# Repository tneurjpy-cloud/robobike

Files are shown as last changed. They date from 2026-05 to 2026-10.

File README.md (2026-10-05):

https://github.com/tneurjpy-cloud/robobike
| Supported Targets | ESP32-C3 |
| --- | --- |

ROBOBIKE: Autonomous Self-Balancing Bicycle Robot  
Copyright 2026.06.05    Masayuki Tanaami      Mobile-Bot Lab. Japan  

ESP-IDF components and tools paths depend on installation location  

* Control Logic
The ROBOBIKE utilizes a dual-loop control system: an outer steering PD loop and an inner roll rate feedback loop to achieve self-balancing via counter-steering.

## Control System Architecture

```mermaid
graph TD
    %% 目標値の入力
    In((str_target)) -- "目標値" --> Sum1((+))

    subgraph OuterLoop [外側：ステアリングPD制御]
        Sum1 -- "偏差" --> GainP[Pゲイン]
        Sum1 -- "偏差" --> Diff[微分+LPF]
        
        GainP --> Sum2((+))
        Diff --> Sum2
    end

    Sum2 -- "目標ロール速度" --> Sum3((+))

    subgraph InnerLoop [内側：ロール速度FB]
        IMU[IMU_roll実測] -. "−" .-> Sum3
        Sum3 -- "偏差" --> GainW[ロールゲイン]
        GainW -- "更新量" --> Integ["積分 & 逆操舵<br>(str_out -= 更新量)"]
    end

    %% 出力とフィードバック
    Integ --> OutP[ステアリング出力 str_out]
    OutP -. "フィードバック" .-> Sum1
    
    OutP --> Limit[リミッタ]
    Limit --> PWM((PWM出力))

    %% スタイルの設定
    style OuterLoop fill:#fdfdfd,stroke:#333
    style InnerLoop fill:#f0f7ff,stroke:#0052cc
    style Integ fill:#e1f5fe,stroke:#01579b

```
## Getting Started

This project is based on "Captive Portal Example".  
Development should be done using ESP-IDF v6.0  
Please install the ESP-IDF extension in VS-Code before building this project.  
  
* How to set up IntelliSense in VS Code:  
(1) Install the ESP-IDF Extension.  
(2) (Ctrl+Shift+P)Run the command "ESP-IDF: Add vscode configuration folder".  
(3) Perform a Build to generate necessary configuration files.  
-----------------------------------------------------------  
* Settings from menuconfig are saved to \project\sdkconfig  
* Change via menuconfig, KCONFIG Name:  
    Flash size : 4MB  
    Partition Table : Custom Partition Table CSV  
        CSV file : partitions.csv  
    configUSE_TRACE_FACILITY : checked  
    configGENERATE_RUN_TIME_STATS : checked
    configTICK_RATE_HZ : 100
* For debug with GDB, delete "launch.json"
    Full Clean
    Select Target to esp32c3 via USB JTAG
    Select COM port, Build and flash
    Power down the target and perform a complete system reboot.
    OpenOCD Server, select "Eclipse CDT..."
    Full Clean
    Slelect Target to esp32c3 via USB JTAG
    Select COM port, Build and flash
    Power down the target and perform a complete system reboot.
    OpenOCD Server, select "Eclipse CDT..."
-----------------------------------------------------------  

* Change Log  
```text
Date        CODE    DATA    Description
------------------------------------------------------------------------------------------------
2026.09.27  1042       6    Add: Test mode on every reset
2026.09.13  1041       6    Dbg: Fix mobile file selection issue on OTA
2026.09.11  1040       6    Dbg: Stop servo PWM during OTA
2026.09.10  1038       6    Dbg: Accept OTA by smartphone
2026.09.02  1037       6    Chg: Captive portal handler(for iPhone)
2026.08.28  1036       6    Chg: Sleep time, minor changes for auto circling mode
2026.07.05  1033       4    Add: Data monitor and its related files.
2026.06.05  1032       4    Dbg: LED control configTICK_RATE_HZ:100
2026.05.26  1031       4    Chg: Servo PWM Rising Times. Lo-pass filter T
2026.05.19  1030    1022    Chg: Axis polarity inversion / No use GPIO Int. for Task
                            Dbg: Monitor.html  
2026.05.06  1029    1022    Chg: 3ms 1-shot soft timer -> 4ms espTimer / STR cmd Polarity +: left
                            Add: Ota, Data monitor.
                            Chg: esp-idf v5.4.1-->> v6.0.1
2026.04.07  1028    1022    Add: WiFi AP Ch. randomize
2026.03.31  1027    1021    Add: BACK cmd, SV EN Cont. heapless buffer
2026.03.20  1025    1021    Mov: GPIO definitions from servo.c to userdefine.h
2026.03.01  1024    1021    Add: IMU data API, 
                            Dbg: Calibration
2026.02.09  1023    1021    Add: Auto circling On/Off, restore SLEEP function
2026.01.20  1022    1021    Add: Speed buttons to control UI, add only_data
2026.01.17  1021    1021    Add: Auto circling
2026.01.11  1020    1020    The 1st release
2025.12.10  1017    1015    Ex1 step: converted to float (smooth side stand movement)
2025.11.29  1016    1015    Add: Steering slide bar
2025.11.11  1014    1014    Suppress UI scaling, add adjustment items, update stop sequence
2025.10.28  1011    1011    Update: Adjustment screen
```

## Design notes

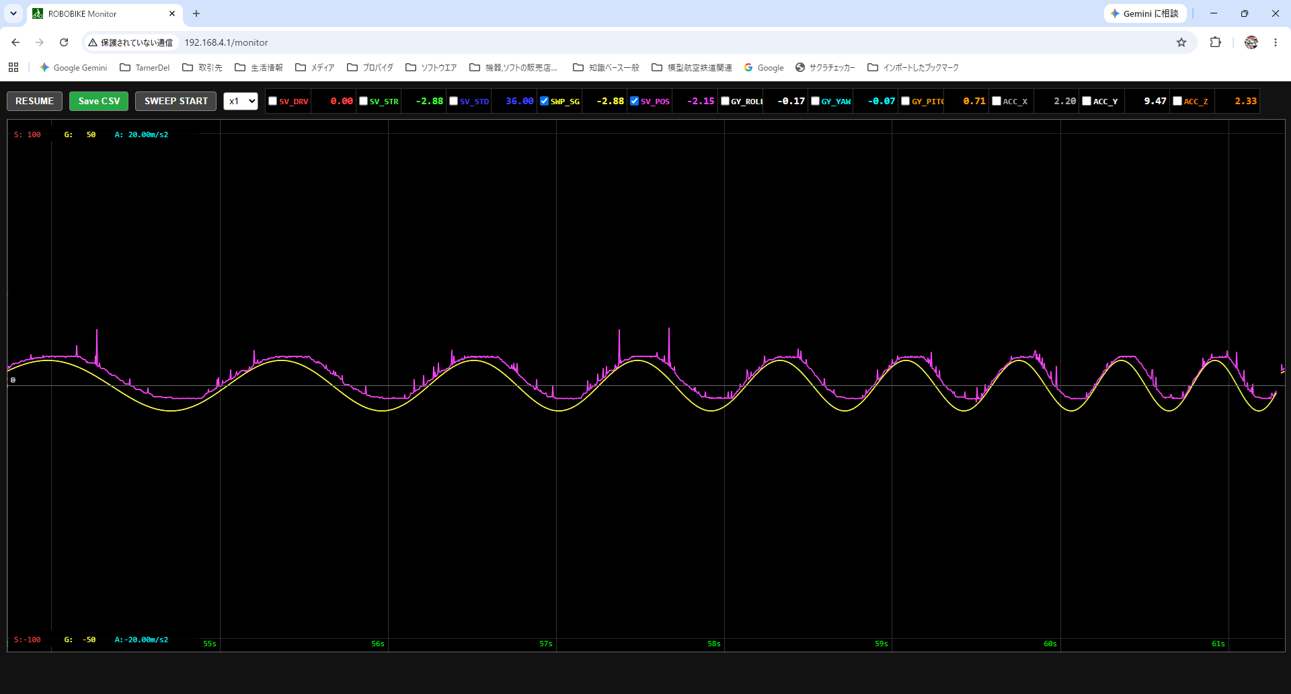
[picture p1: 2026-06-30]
doc/monitor.png

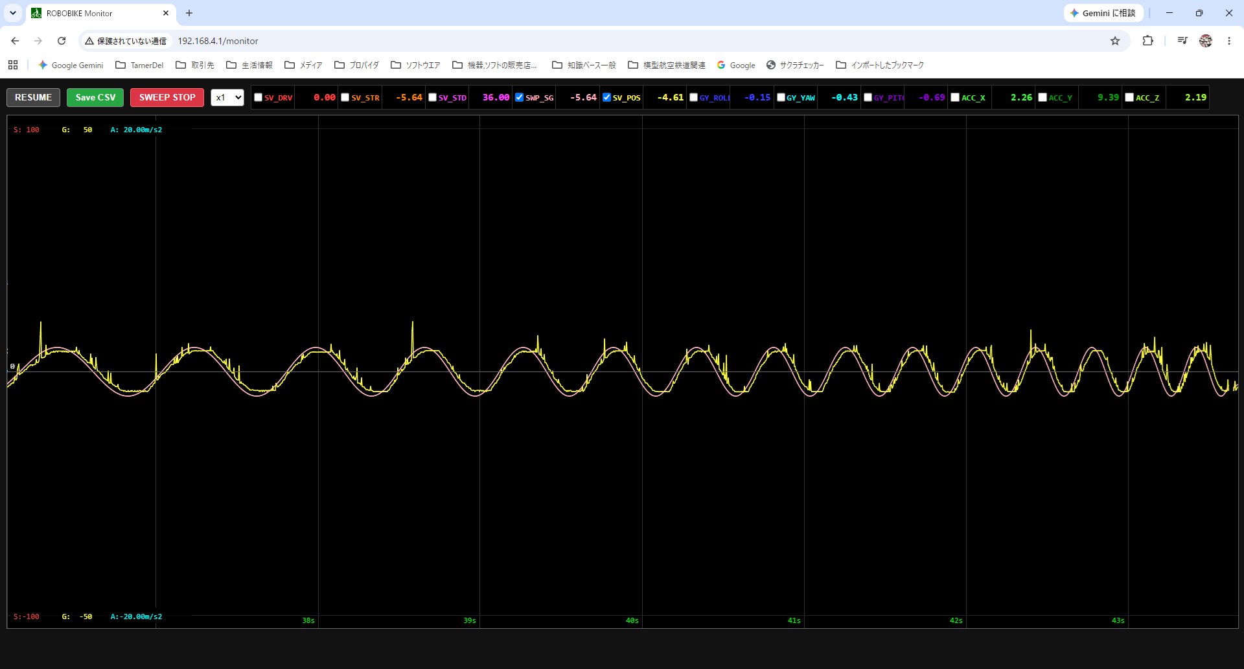
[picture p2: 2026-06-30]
doc/monitor2.png

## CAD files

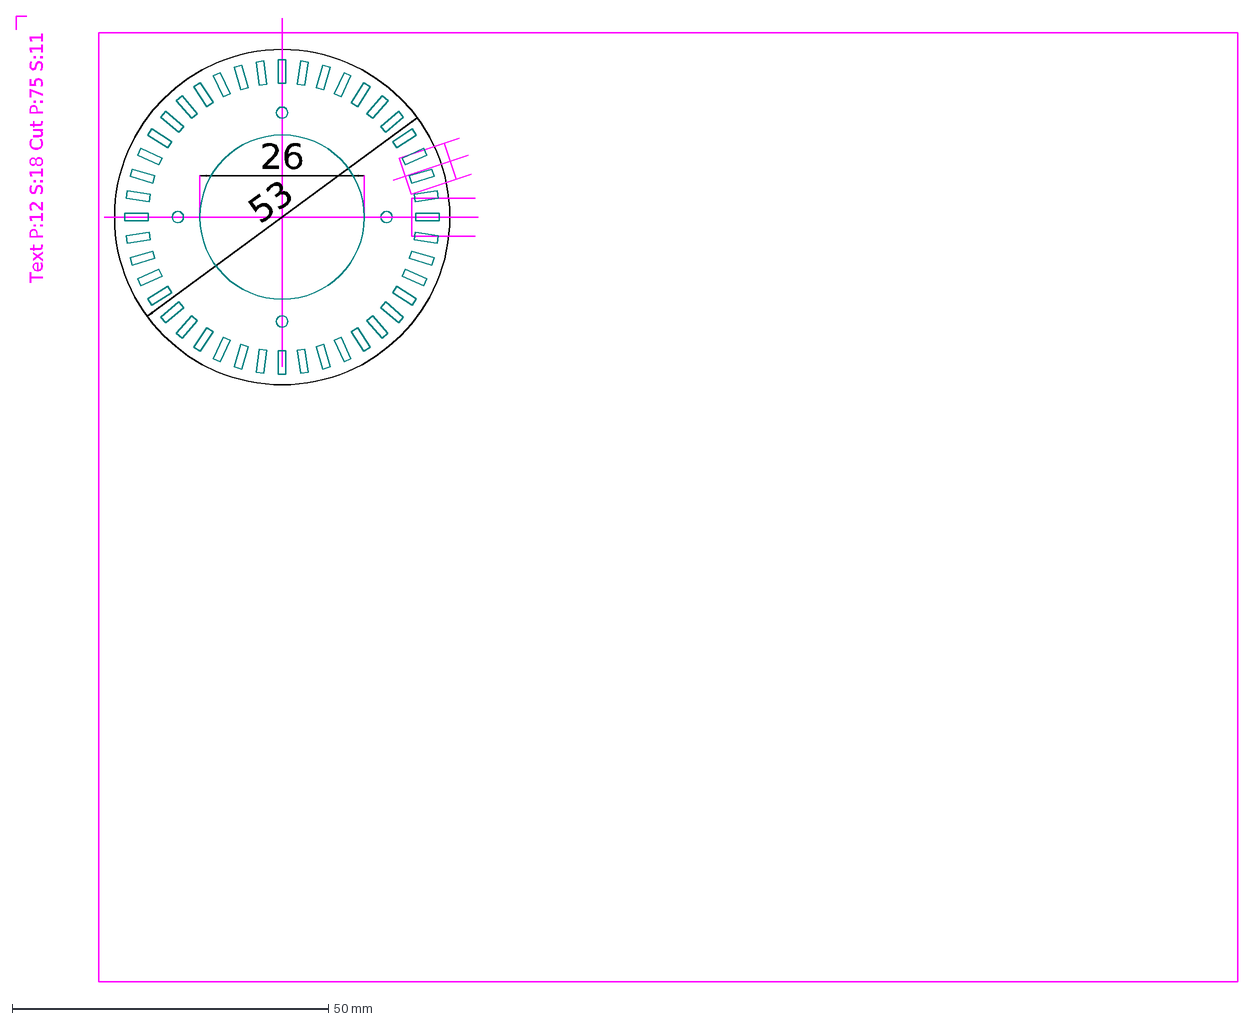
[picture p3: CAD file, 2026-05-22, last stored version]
hardware/DXF/slitring.dxf
Text P:12 S:18 Cut P:75 S:11
53
26

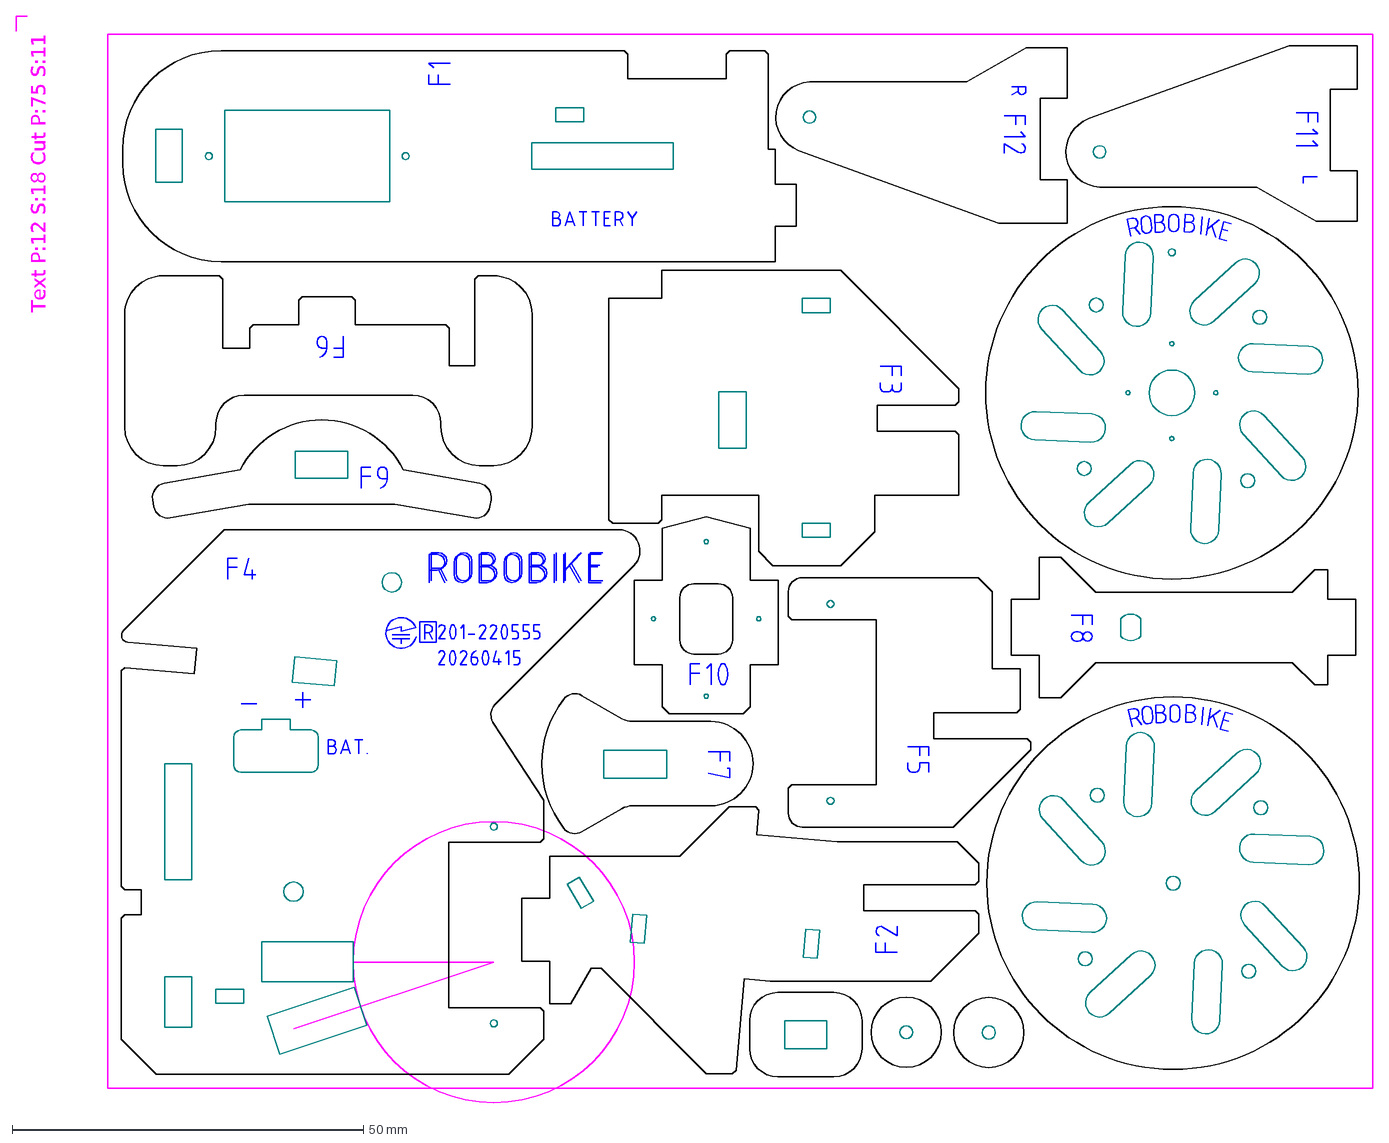
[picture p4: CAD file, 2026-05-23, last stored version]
hardware/DXF/20260522_1p.dxf
Text P:12 S:18 Cut P:75 S:11

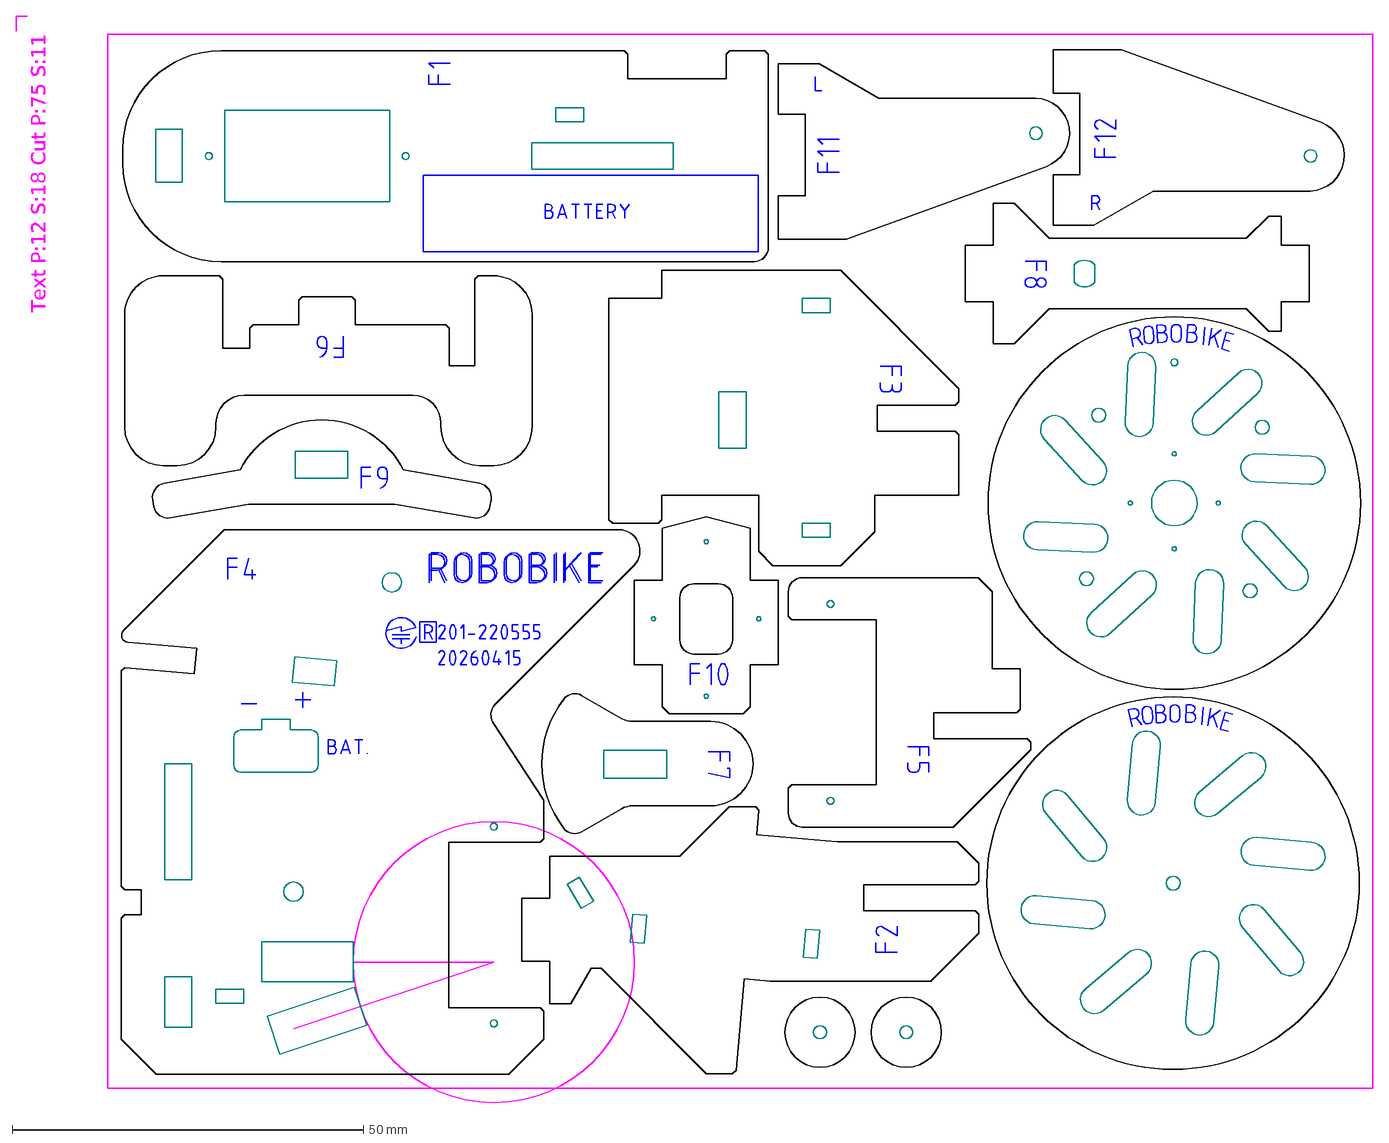
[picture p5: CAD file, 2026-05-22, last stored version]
hardware/DXF/20260407_1p.dxf
Text P:12 S:18 Cut P:75 S:11

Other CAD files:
hardware/DXF/#20260522_1p.dxf

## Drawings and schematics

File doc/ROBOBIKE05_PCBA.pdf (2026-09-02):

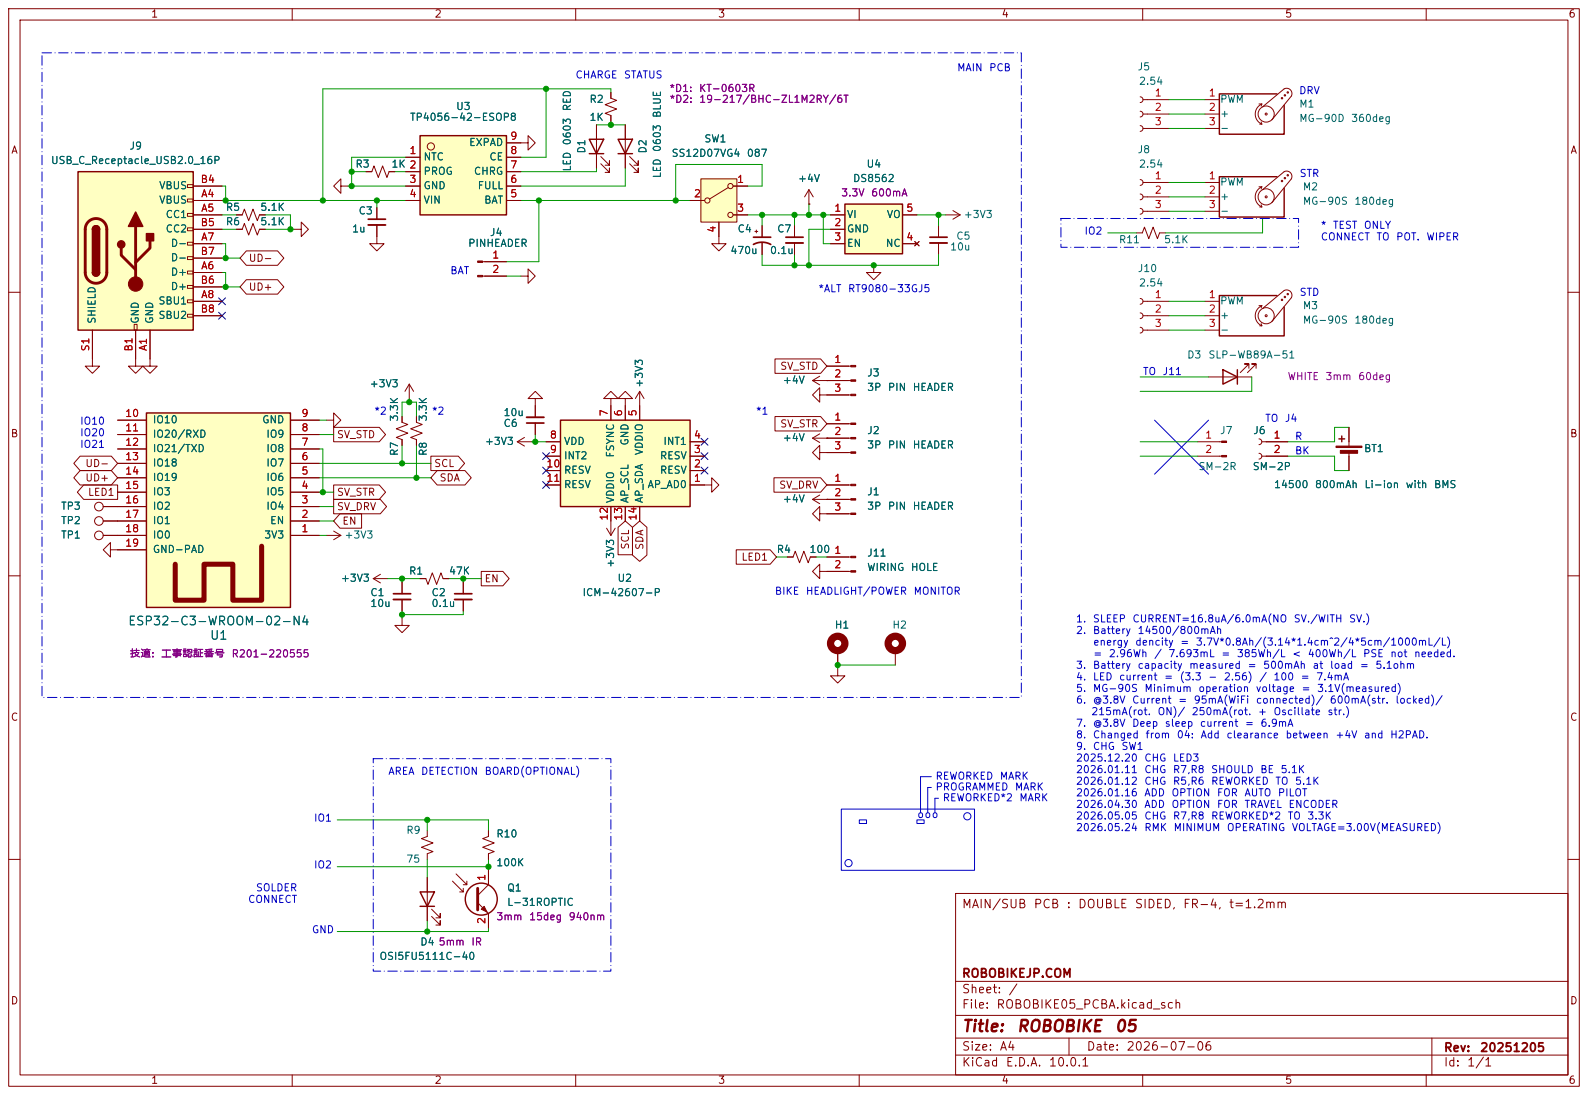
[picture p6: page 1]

* TEST ONLY CONNECT TO POT. WIPER

BIKE HEADLIGHT/POWER MONITOR

1. SLEEP CURRENT=16.8uA/6.0mA(NO SV./WITH SV.) 2. Battery 14500/800mAh

energy dencity = 3.7V*0.8Ah/(3.14*1.4cm^2/4*5cm/1000mL/L) = 2.96Wh / 7.693mL = 385Wh/L < 400Wh/L PSE not needed. 3. Battery capacity measured = 500mAh at load = 5.1ohm

4. LED current = (3.3 - 2.56) / 100 = 7.4mA 5. MG-90S Minimum operation voltage = 3.1V(measured) 6. @3.8V Current = 95mA(WiFi connected)/ 600mA(str. locked)/

215mA(rot. ON)/ 250mA(rot. + Oscillate str.) 7. @3.8V Deep sleep current = 6.9mA 8. Changed from 04: Add clearance between +4V and H2PAD. 9. CHG SW1

2025.12.20 CHG LED3
2026.01.11 CHG R7,R8 SHOULD BE 5.1K
2026.01.12 CHG R5,R6 REWORKED TO 5.1K
2026.01.16 ADD OPTION FOR AUTO PILOT 2026.04.30 ADD OPTION FOR TRAVEL ENCODER

2026.05.05 CHG R7,R8 REWORKED*2 TO 3.3K
2026.05.24 RMK MINIMUM OPERATING VOLTAGE=3.00V(MEASURED)

MAIN/SUB PCB : DOUBLE SIDED, FR-4, t=1.2mm

Size: A4 | Rev: 20251205
KiCad E.D.A. 10.0.1 | Id: 1/1

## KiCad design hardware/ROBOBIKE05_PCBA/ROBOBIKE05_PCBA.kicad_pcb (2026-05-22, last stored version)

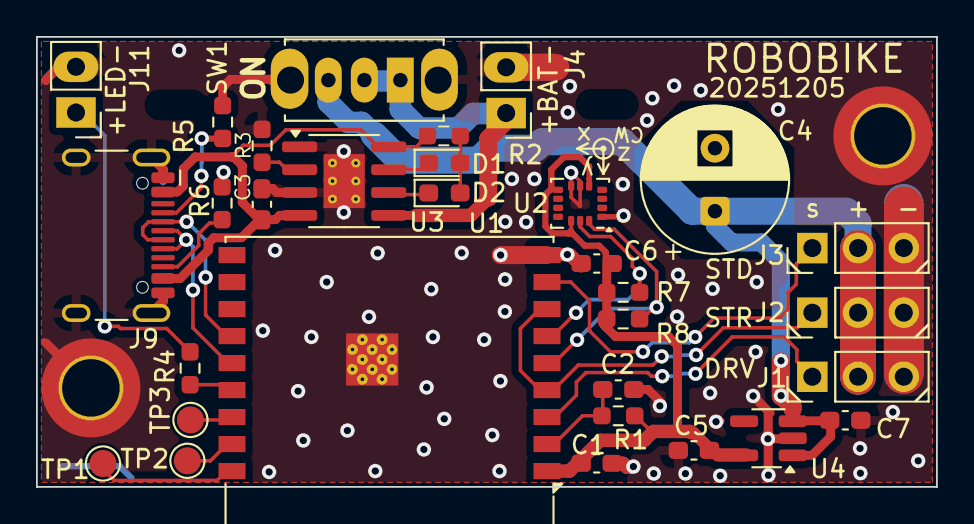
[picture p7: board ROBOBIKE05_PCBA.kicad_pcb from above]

Board: 2 copper layers, 50.0 x 25.0 mm, 33 parts (0 on the bottom side), 24 nets.

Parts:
C1, C5, C6: 10u; C_0603_1608Metric_Pad1.08x0.95mm_HandSolder
C2, C7: 0.1u; C_0603_1608Metric_Pad1.08x0.95mm_HandSolder
C3: 1u; C_0603_1608Metric_Pad1.08x0.95mm_HandSolder
C4: 470u; CP_Radial_D8.0mm_P3.50mm
D1: LED 0603 RED; LED_0603_1608Metric_Pad1.05x0.95mm_HandSolder
D2: LED 0603 BLUE; LED_0603_1608Metric_Pad1.05x0.95mm_HandSolder
H1, H2: MountingHole_Pad; MountingHole_3.2mm_M3_ISO14580_Pad_TopBottom
J1, J2, J3: 3P PIN HEADER; PinHeader_1x03_P2.54mm_Vertical
J4, J11: WIRING HOLE; PinHeader_1x02_P2.54mm_Vertical
J9: USB_C_Receptacle_USB2.0_16P; USB_C_Receptacle_HCTL_HC-TYPE-C-16P-01A
R1: 47K; R_0603_1608Metric_Pad0.98x0.95mm_HandSolder
R2, R3: 1K; R_0603_1608Metric_Pad0.98x0.95mm_HandSolder
R4: 100; R_0603_1608Metric_Pad0.98x0.95mm_HandSolder
R5, R6, R7, R8: 5.1K; R_0603_1608Metric_Pad0.98x0.95mm_HandSolder
SW1: SS12D07VG4 087; SW_Slide_SPDT_Straight_CK_OS102011MS2Q
TP1, TP2, TP3: TestPoint_Pad_D1.5mm
U1: ESP32-C3-WROOM-02-N4; ESP32-C3-WROOM-02
U2: ICM-42607-P; LGA-16_3x3mm_P0.5mm_LayoutBorder3x5y
U3: TP4056-42-ESOP8; SOIC-8-1EP_3.9x4.9mm_P1.27mm_EP2.29x3mm_ThermalVias
U4: DS8562; SOT-23-5_HandSoldering

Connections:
+3V3: C1.1, C5.1, C6.1, R1.1, R7.2, R8.2, U1.1 (3V3), U2.5 (VDDIO), U2.8 (VDD), U2.12 (VDDIO), U4.5 (VO)
+4V: C4.1, C7.1, J1.2, J2.2, J3.2, SW1.3 (C), U4.1 (VI), U4.3 (EN)
EN: C2.1, R1.2, U1.2 (EN)
GND: C1.2, C2.2, C3.2, C4.2, C5.2, C6.2, C7.2, H1.1, H2.1, J1.3, J2.3, J3.3, J4.2, J9.A1 (GND), J9.B1 (GND), J9.S1 (SHIELD), J11.2, R3.1, R5.1, R6.1, SW1.4 (FR), U1.9 (GND), U1.19 (GND-PAD), U2.1 (AP_AD0), U2.6 (GND), U2.7 (FSYNC), U3.1 (NTC), U3.3 (GND), U3.9 (EXPAD), U4.2 (GND)
LED1: R4.1, U1.15 (IO3)
unnamed: D1.2 (A), D2.2 (A), R2.1
unnamed: D1.1 (K), U3.7 (CHRG)
unnamed: D2.1 (K), U3.6 (FULL)
unnamed: J4.1, SW1.1 (A), SW1.2 (B), U3.5 (BAT)
unnamed: J9.A5 (CC1), R5.2
unnamed: J9.B5 (CC2), R6.2
unnamed: J11.1, R4.2
unnamed: TP1.1, U1.18 (IO0)
unnamed: TP2.1, U1.17 (IO1)
unnamed: TP3.1, U1.16 (IO2)
unnamed: C3.1, J9.A4 (VBUS), J9.B4 (VBUS), R2.2, U3.4 (VIN), U3.8 (CE)
unnamed: R3.2, U3.2 (PROG)
SCL: R7.1, U1.6 (IO7), U2.13 (AP_SCL)
SDA: R8.1, U1.5 (IO6), U2.14 (AP_SDA)
SV_DRV: J1.1, U1.3 (IO4)
SV_STD: J3.1, U1.8 (IO9)
SV_STR: J2.1, U1.4 (IO5), U1.7 (IO8)
UD+: J9.A6 (D+), J9.B6 (D+), U1.14 (IO19)
UD-: J9.A7 (D-), J9.B7 (D-), U1.13 (IO18)

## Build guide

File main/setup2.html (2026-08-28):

## ROBOBIKE ADVANCED SETUP

STEERING GAIN ---

↑ ↓

ROLLING GAIN ---

↑ ↓

DIFFERENTIAL GAIN ---

↑ ↓

YAW COEFF. ---

↑ ↓

STR CMD SPD ---

↑ ↓

AUTO CIRC GAIN ---

↑ ↓

LOAD DEFAULT VALUES

OK CANCEL

AUTO CIRCLING

LOAD DEFAULT EXIT

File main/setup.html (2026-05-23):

PROGVER ---

## ROBOBIKE SETUP

STEERING NEUTRAL ---

← →

STEERING MAX ---

↑ ↓

STARTING TILT ANGLE ---

← →

DRIVE SPEED ---

↑ ↓ STOP

ADVANCED SETTINGS DATA MONITOR PROGRAM UPDATE SAVE & EXIT

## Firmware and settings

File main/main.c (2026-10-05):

/*
    ROBOBIKE with WiFi captive portal
*/

#include "userdefine.h"

static const char *TAG = "main";

////////////////////////////////////////////////////////////////////////
void check_sleep_indicator(void)
{
    esp_sleep_source_t cause = esp_sleep_get_wakeup_causes();

    if (cause != ESP_SLEEP_WAKEUP_ALL)
    { // 450ms to do reset to shutdown
        gpio_reset_pin(LED_GPIO);
        gpio_set_direction(LED_GPIO, GPIO_MODE_OUTPUT);

        // 一瞬ピカッと光らせる（例: 30msだけ点灯）
        gpio_set_level(LED_GPIO, 1);
        vTaskDelay(pdMS_TO_TICKS(30));
        gpio_set_level(LED_GPIO, 0);

        // 再び10秒のタイマー設定をしてディープスリープへ戻る
        esp_sleep_enable_timer_wakeup(SLEEPINTERVAL * 1000ULL); // usec
        esp_deep_sleep_start();
    }
}

void deviceCheck()
{
    // str
    set_str_cmd(15.0f, 0.0f);
    waitms(250);
    set_str_cmd(0.0f, 0.0f);
    waitms(250);

    // mot
    set_mot_duty(10.0f, 0.0f);
    waitms(150);
    set_mot_duty(0.0f, 0.0f);
    waitms(250);

    // ex1
    set_ex1_angle(saved.ang_std_nut + STD_STD_NUT + 10.0f, 0.0f);
    waitms(250);
    set_ex1_angle(saved.ang_std_nut + STD_STD_NUT, 0.05f);
}

void app_main(void)
{
    int maxcount = 0;
    uint32_t lastdone;

    check_sleep_indicator();

    esp_log_level_set("*", ESP_LOG_INFO);
    ESP_LOGI(TAG, "Start ROBOBIKE system");

    userdeviceinit();
    if (IMU_init() != ESP_OK)
    {
        ESP_LOGE(TAG, "Failed to initialize IMU");
        while (true)
        {
            set_led_brightness(LEDHIGH);
            waitms(125);
            set_led_brightness(LEDOFF);
            waitms(125);
        }
    }

    servo_init();
    webserver_start();

    deviceCheck();

    set_led_brightness(LEDLOW);
    // set_str_cmd(0.0f, 100.0f);
    printf("PROGVER=%d DATAVER=%u SYSID=%s\n", PROGVER, DATAVER, SysID());
    ESP_LOGI(TAG, "OpTime=%lusec\n", saved.op_time_s);
    showTasks();

    lastdone = millis();
    for (;;)
    {
        waitms(100);

        if (auto_en && (str_out >= (STRMAX - 2) || str_out <= -(STRMAX - 2)))
        { // 転倒判定
            extern uint32_t duty_str_prev;
            ESP_LOGI(TAG, "Str duty_s1=%lu", duty_str_prev);
            if (maxcount >= 5)
            {
                auto_disable();
                set_mot_duty(0.f, 0.f);
                waitms(100);
                set_ex1_angle(saved.ang_std_nut + STD_STD_NUT, 0.1f);
                set_str_cmd(0.f, 0.5f);
                maxcount = 0;
                set_led_brightness(LEDLOW);
            }
            else
            {
                maxcount++;
            }
        }
        else
        {
            maxcount = 0;
        }

        if (isNms(&lastdone, 1000))
        {
            if ((mot_out == 0.0f) && ((millis() - userLastControlTime) >= SLEEP_DURATION_MS))
            {
                deepSleep(SLEEPINTERVAL);
            }
        }
    }
}

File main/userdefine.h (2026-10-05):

/*////////////////////////////////////////////////////////////////////////////////
userdefine.h        ROBOBIKE project

Copyright 2026.09.27  ROBOBIKEJP M.Tanaami
////////////////////////////////////////////////////////////////////////////////*/

#pragma once

#define PROGVER 1042 // version for program
#define DATAVER 6    // version for saved data in NVS

#include <stdint.h>
#include <stdbool.h>
#include <math.h>
#include <stdatomic.h>

#include <driver/gpio.h>
#include <driver/ledc.h>
#include <driver/gptimer.h>
#include <driver/i2c_master.h>
#include <freertos/FreeRTOS.h>
#include <freertos/task.h>
#include <freertos/timers.h>
#include <lwip/inet.h>
#include <lwip/sockets.h>

#include <esp_attr.h>
#include <esp_check.h>
#include <esp_err.h>
#include <esp_event.h>
#include <esp_http_server.h>
#include <esp_log.h>
#include <esp_mac.h>
#include <esp_netif.h>
#include <esp_sleep.h>
#include <esp_timer.h>
#include <esp_ota_ops.h>
#include <esp_partition.h>
#include <esp_system.h>
#include <esp_wifi.h>
#include <nvs.h>
#include <nvs_flash.h>
#include <dns_server.h>
#include "esp_adc/adc_oneshot.h"

#include "IMU.h"

#define ESP_WIFI_PASS ""

///////////////// GPIO use ////////////////
#define IO_0 0
#define IO_1 1
#define IO_2 2 // OUT Hi on PWON RESET
#define IO_3 3 // LED Hi:ON Lo:OFF
#define IO_4 4
#define IO_5 5
#define IO_6 6
#define IO_7 7
#define IO_8 8 // OUT Hi on PWON RESET
#define IO_9 9 // OUT Hi on PWON RESET
#define IO_10 10
#define IO_20 20
#define IO_21 21

#define LED_GPIO IO_3
#define I2C_MASTER_SCL_IO IO_7
#define I2C_MASTER_SDA_IO IO_6
#define GPIO_DRV IO_4
#define GPIO_STR IO_5
#define GPIO_STR_IN IO_8
#define GPIO_EX1 IO_9
#define IMU_INT0 IO_10

///////////////// R/C servo using /////////////////
#define SERVO_NEUTRAL_DUTY (1500.0f) // 0deg 1500us
#define STR_ADJ_MIN (-90)            //
#define STR_ADJ_MAX (90)             //
#define STR_SLIDER_MAX 100.0f        // +-100
#define STR_GA_MAX 0.200f            //
#define STR_GA_MIN 0.001f            //
#define DIFF_GA_MAX 0.200f           //
#define DIFF_GA_MIN 0.000f           //
#define ROLL_GA_MAX 60               //
#define ROLL_GA_MIN 1                //
#define ANG2PULSE (1000.0f / 90.0f)  //

#define AUTOCORRECTTIME 150 // msec

typedef struct
{
    union
    {
        struct
        {
            int ver;              // data ver
            uint32_t op_time_s;   // operation time in minutes
            bool isChecked;       //
            float gain_str;       // delta = 0.01
            float gain_str_diff;  //
            float gain_w_roll;    // delta = 1.0
            Tvector6d acc_offset; //
            Tvector6d acc_dir;    //
            float str_diff_alph;  // alpha for low-pass filter of str_dev_diff
            int str0;             //
            int mot_spd;          //
            int ang_std_nut;      //
            float run_coeff;      // run-speed feedback coefficient
            float yaw_coeff;      // yaw‑rate feedback coefficient
            int str_turn;         //
            int str_cmd_speed;    // steering command changeing speed deg/sec
            bool autoCircling;    // auto circling mode
            float auto_circ_gain; // auto circling Gain(0.0-1.0)
        };
        uint8_t payloadArea[256 - sizeof(uint32_t)]; //
    };
    uint32_t CRC; //
} TSave;

typedef enum         // 自動旋回修正用状態定義
{                    //
    rsOuter,         // 外側走行、定常旋回
    rsInner_Correct, // 内側走行、修正動作
    rsInner_Stable   // 内側走行、定常旋回
} TRunState;

#define STRMAX 80
#define STR_STOP 40
#define MOTMAX 60 // MG90D max duty = 90%,21.1kHz @50deg()
#define MOT_SPEED_BACK (-20)
#define EX1MAX 60
#define EX1MIN (-10)
#define STD_RUN 100
#define STD_STD_NUT 16 // diff STD. - NUT.

#define RING_BUF_SIZE (SAMPLE_RATE_HZ * 5) // for data monitor
#define CTL_DATA_BUFSIZE (65536)           //

#define LEDHIGH 255
#define LEDLOW 32
#define LEDOFF 0
#define SLEEPINTERVAL (10 * 1000UL)          // 10 sec to sleep
#define SLEEP_DURATION_MS (15 * 60 * 1000UL) // 15min to sleep
#define millis() ((uint32_t)(esp_timer_get_time() / 1000))
#define waitTaskms(xms) vTaskDelay(pdMS_TO_TICKS(xms))

extern float mot_cmd;    // -100 <> +100%
extern float mot_step;   // %/step
extern float mot_out;    // extern float str_cmd0; // -180 / +180 deg
extern float str_cmd0;   // -180.0f / +180.0f deg  > 0.0: turn right
extern float str_cmd1;   // -180 / +180 deg
extern float str_target; // -180 / +180 deg
extern float str_out;    // -180 / +180 deg
extern float ex1_cmd;    // -180 / +180 deg
extern float ex1_out;    // -180 / +180 deg

extern TSave saved;
extern const TSave savedefault;

extern bool auto_en;

extern volatile uint32_t userLastControlTime;

extern volatile bool stopServo;
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

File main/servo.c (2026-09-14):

/*//////////////////////////////////////////////////////////////////////////
    servo.c

サーボ制御用タイマーchart (4ステージ・4000usフレーム・全サーボ相乗り版)

    == : H level
    __ : L level or stop
    -- : count up running, waiting
    +  : start
    |  : fire interrupt

LEDC_CHANNEL_1, 0, 2 --> GPIO_STR, DRV, EX1 (s1 duty可変0-100%)
           s0           s1            s2          s3
____+============+======_______+____________+____________+=====
        1000us    500us  500us     1000us       1000us

GPIO_STR_IN <-- GPIO_STR external interrupt 4ms interval
    cbPulseIn
____|____________________________________________________|_____
    start sync_timer

sync_timer(gptimer)
CB         cb0          cb1           cb2          cb3
____+------|------------|-------------|------------|_____+-----
    0     400us        1400us        2400us       3400us
    FIRSTWT  STGINTRVL    STGINTRVL    STGINTRVL

CallBackFunctions
cbStrIn: (GPIO external interrupt)
  FIRSTWTus後にcb0を起動するようsync_timerを開始

cb0: (gptimer countup interrupt)
  ControlTask起床
  IMUのデータ取り込みを行い、全サーボの計算、
  str,mot s1のduty=0-50% を書き出し
  stdサーボのs0のduty=100%を書き出し
  1000us後のtimer割り込みをスタート

cb1: (gptimer countup interrupt)
  std s1のduty=0-50% を書き出し
  str,motサーボのs2のduty=0%を書き出し
  1000us後のtimer割り込みをスタート

cb2: (gptimer countup interrupt)
  stdサーボのs2のduty=0%を書き出し
  1000us後のtimer割り込みをスタート

cb3: (gptimer countup interrupt)
  str,motサーボのs0のduty=100%を書き出し
  sync_timerは停止

//////////////////////////////////////////////////////////////////////////*/

#include "userdefine.h"

static const char TAG[] = "servo";

float str_cmd0;   // deg +-90.0f  +: Left turn
float str_cmd1;   // deg
float str_target; // deg
float str_step;   // deg/cycle
float str_out;    // deg

float mot_cmd;  // % +-100.0f
float mot_step; // %/cycle
float mot_out;  // %

float ex1_cmd;  // deg +-90.0f
float ex1_out;  // deg
float ex1_step; // deg/cycle

TSave saved;
float *pyaw_coeff;
volatile bool stopServo = false;

const TSave savedefault = {
    .ver = DATAVER,                                        // (int) data format version
    .op_time_s = 0,                                        // (uint32_t) operation time in sec
    .isChecked = false,                                    // isChecked
    .gain_str = 0.030f,                                    // gain_str;
    .gain_str_diff = 0.030f,                               // gain_str_diff
    .gain_w_roll = 12.0f,                                  // gain_w_roll;
    .acc_offset = {0.0f, 0.0f, 0.0f, 0.0f, 0.0f, 0.0f},    // acc_offset
    .acc_dir = {0.0f, 0.0f, 0.0f, 0.0175f, 0.9996f, 0.0f}, // acc_dir
    .str_diff_alph = 0.040f,                               // str_diff_alph
    .str0 = 0,                                             // (int) steering angle neutral R= +deg
    .mot_spd = 60,                                         // (int) motor speed 0-99 (88.5RPM/4.0V, 57.9RPM/SPD=10)
    .ang_std_nut = 20,                                     // (int) stand for start
    .run_coeff = 0.0f,                                     // run-speed feedback coefficient
    .yaw_coeff = 0.011f,                                   // yaw‑rate feedback coefficient
    .str_turn = 40,                                        // (int) str_turn deg
    .str_cmd_speed = 30,                                   // (int) str_cmd_speed deg/sec
    .autoCircling = false,                                 // (bool) autoCircling
    .auto_circ_gain = 0.75f                                // (float) autoCirclingGain
};

//// R/C servo pulse width making
#define TIMER_RES_HZ 1000000 //
#define PWM_DUTY_0 0         //
#define PWM_DUTY_100 4096    // 12bit完全100%固定値
#define PWM_STAGE_LEN 1000   // us
#define PWM_MAXLEN 1990      // us
#define PWM_MINLEN 1010      // us
#define CB0DELAY 10          // us
#define FIRSTWT 400          // us
#define STG_INTRVL 1000      // us

/* 全サーボ共通：12bit高精度タイマーへ一本化 */
static const ledc_timer_config_t servo_timer_str = {
    .speed_mode = LEDC_LOW_SPEED_MODE,
    .duty_resolution = LEDC_TIMER_12_BIT, // 4096 steps for 100% duty
    .timer_num = LEDC_TIMER_1,
    .freq_hz = SV_FRQ * 4, // 250Hz * 4 = 1000Hz (1ステージ1000us)
    .clk_cfg = LEDC_AUTO_CLK};

static ledc_channel_config_t svch_mot = {
    .speed_mode = LEDC_LOW_SPEED_MODE,
    .channel = LEDC_CHANNEL_0,
    .timer_sel = LEDC_TIMER_1,
    .intr_type = LEDC_INTR_DISABLE,
    .gpio_num = GPIO_DRV,
    .duty = PWM_DUTY_100, // 初期状態のs0は100%（H開始）
    .hpoint = 0};

static ledc_channel_config_t svch_str = {
    .speed_mode = LEDC_LOW_SPEED_MODE,
    .channel = LEDC_CHANNEL_1,
    .timer_sel = LEDC_TIMER_1,
    .intr_type = LEDC_INTR_DISABLE,
    .gpio_num = GPIO_STR,
    .duty = PWM_DUTY_100, // 初期状態のs0は100%（H開始）
    .hpoint = 0};

static ledc_channel_config_t svch_ex1 = {
    .speed_mode = LEDC_LOW_SPEED_MODE,
    .channel = LEDC_CHANNEL_2,
    .timer_sel = LEDC_TIMER_1,
    .intr_type = LEDC_INTR_DISABLE,
    .gpio_num = GPIO_EX1,
    .duty = PWM_DUTY_0, // ★スタンドは1ステージ遅らせるため、初期状態のs0は0%（L開始）
    .hpoint = 0};

// gpTimer for synchronization
typedef enum // servo sync timer callback step
{
    cb0 = 0,
    cb1,
    cb2,
    cb3,
} TSyncCBStep;

static volatile TSyncCBStep sync_step = cb0;
static gptimer_handle_t sync_timer;
static TaskHandle_t xControlTaskHandle;

// タスクが計算した std（ex1）のs2用可変Dutyを一時保持するバッファ変数
static volatile uint32_t duty_ex1_s2 = 0;

// ★遅刻時の2000usパルス化を防ぐための、前回計算値保持用変数
uint32_t duty_str_prev = 2048; // 初期値ニュートラル(1500us相当)
static uint32_t duty_mot_prev = 2048; // 初期値ニュートラル(1500us相当)

#include <math.h>

// for sin wave sweep ////////////////////////////////////////////////////
#define DT (1.0f / SV_FRQ) // サンプリング周期 (ms)
#define START_FREQ 0.3f    // 開始周波数 (Hz)
#define END_FREQ 40.0f     // 終了周波数 (Hz)
#define SWEEP_TIME 30.0f   // スイープ時間
#define TWO_PI 6.2831853f  // 2pai rad
#define SWEEP_W 5.0f       // sweep width(deg)

bool doSweep = false;
float current_time = 0.0f; // sec
float sweep_phase = 0.0f;
float current_freq = START_FREQ;
float freq_multiplier = 1.0f;
float swp_sg = 0.0f;
float swp_ampletude;

//////////////////////////////////////////////////////////////////////////
void init_sweep()
{
    sweep_phase = 0.0f;
    current_time = 0.0f;
    doSweep = true;
    current_freq = START_FREQ;
    sweep_phase = 0.0f;
    float total_steps = SWEEP_TIME / DT;
    // K = (END_FREQ / START_FREQ) ^ (1 / total_steps)
    freq_multiplier = powf(END_FREQ / START_FREQ, 1.0f / total_steps);
    swp_ampletude = SWEEP_W;
    if (mot_out != 0.0f)
        swp_ampletude *= 0.01f;
}
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

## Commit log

2026-05-22 1031 4ms IMU gain debug
    [#20260522_1p.dxf, 20260407_1p.dxf, 20260522_1p.dxf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]
2026-05-22 I2c asynchronous
2026-05-23 str cmd speed adjust
    [#20260522_1p.dxf, 20260522_1p.dxf]
2026-05-24 diff Lopass coeff chg
    [ROBOBIKE05_PCBA.kicad_sch]
2026-05-25 GDB usage
    [ROBOBIKE05_PCBA.kicad_sch]
2026-06-04 1032 dbg LED drive
2026-06-19 use external Interrupt
    [ROBOBIKE05_PCBA.kicad_sch]
2026-06-20 use 2-stage timer int
2026-06-21 4-stage PWM frame/get small endian IMU data
2026-06-22 remove sch
    [BOM-ROBOBIKE05_PCBA.csv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]
2026-06-24 IMU read debug servo INTERLEAVED
2026-06-26 SV_POS ADC logging
2026-06-28 Bode Plotter
    [20260629063139.csv]
2026-06-30 add description of plotter
    [20260629063139.csv, 20260629180053.csv, 20260630155820.csv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]
